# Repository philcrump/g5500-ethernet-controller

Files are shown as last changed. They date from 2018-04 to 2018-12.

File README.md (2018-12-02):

# G-5500 Ethernet Rotator Controller 

This project exists as firmware and a 'shield' board on an ST NUCLEO-STM32F429ZI Development Board.

The firmware exposes a web server on port 80, through which the rotator can be monitored and commanded.

This project is built on ChibiOS 17.6.x with LwIP 1.4.1

<p float="left">
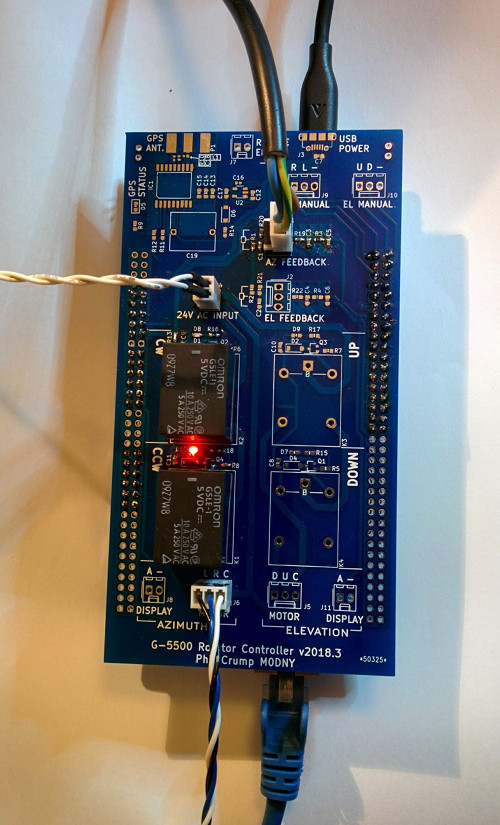
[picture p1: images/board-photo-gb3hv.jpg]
  
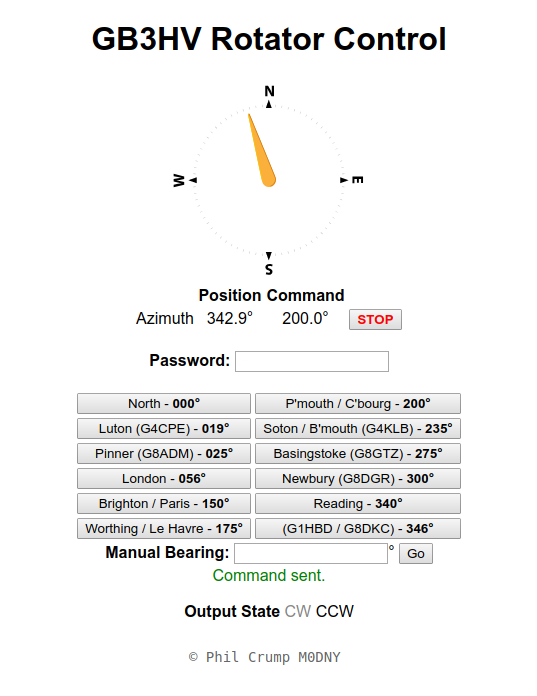
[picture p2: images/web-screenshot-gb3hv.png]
  
</p>

## Wiring

**J1** - "AZ FEEDBACK"
1. G-5500 Azimuth Pin 1 (Feedback Rheostat 360-end)
2. G-5500 Azimuth Pin 2 (Feedback Rheostat Wiper)
3. G-5500 Azimuth Pin 3 (Feedback Rheostat 0-end)

**J6** - "AZIMUTH" -> "MOTOR"
1. (L) G-5500 Azimuth Pin 4 (Motor Winding 1)
2. (R) G-5500 Azimuth Pin 5 (Motor Winding 2)
3. (C) G-5500 Azimuth Pin 6 (Motor Center Tap)

## TODO

- [x] Flash Storage of settings (on settings branch)
- [ ] Interface to edit presets

### Possible future features

- [ ] Merge in satellite tracking computations from old project (using NTP, GPS, & libpredict)
- [ ] Update to ChibiOS 18.2.x (There seems to be a DHCP Client bug - needs investigation)

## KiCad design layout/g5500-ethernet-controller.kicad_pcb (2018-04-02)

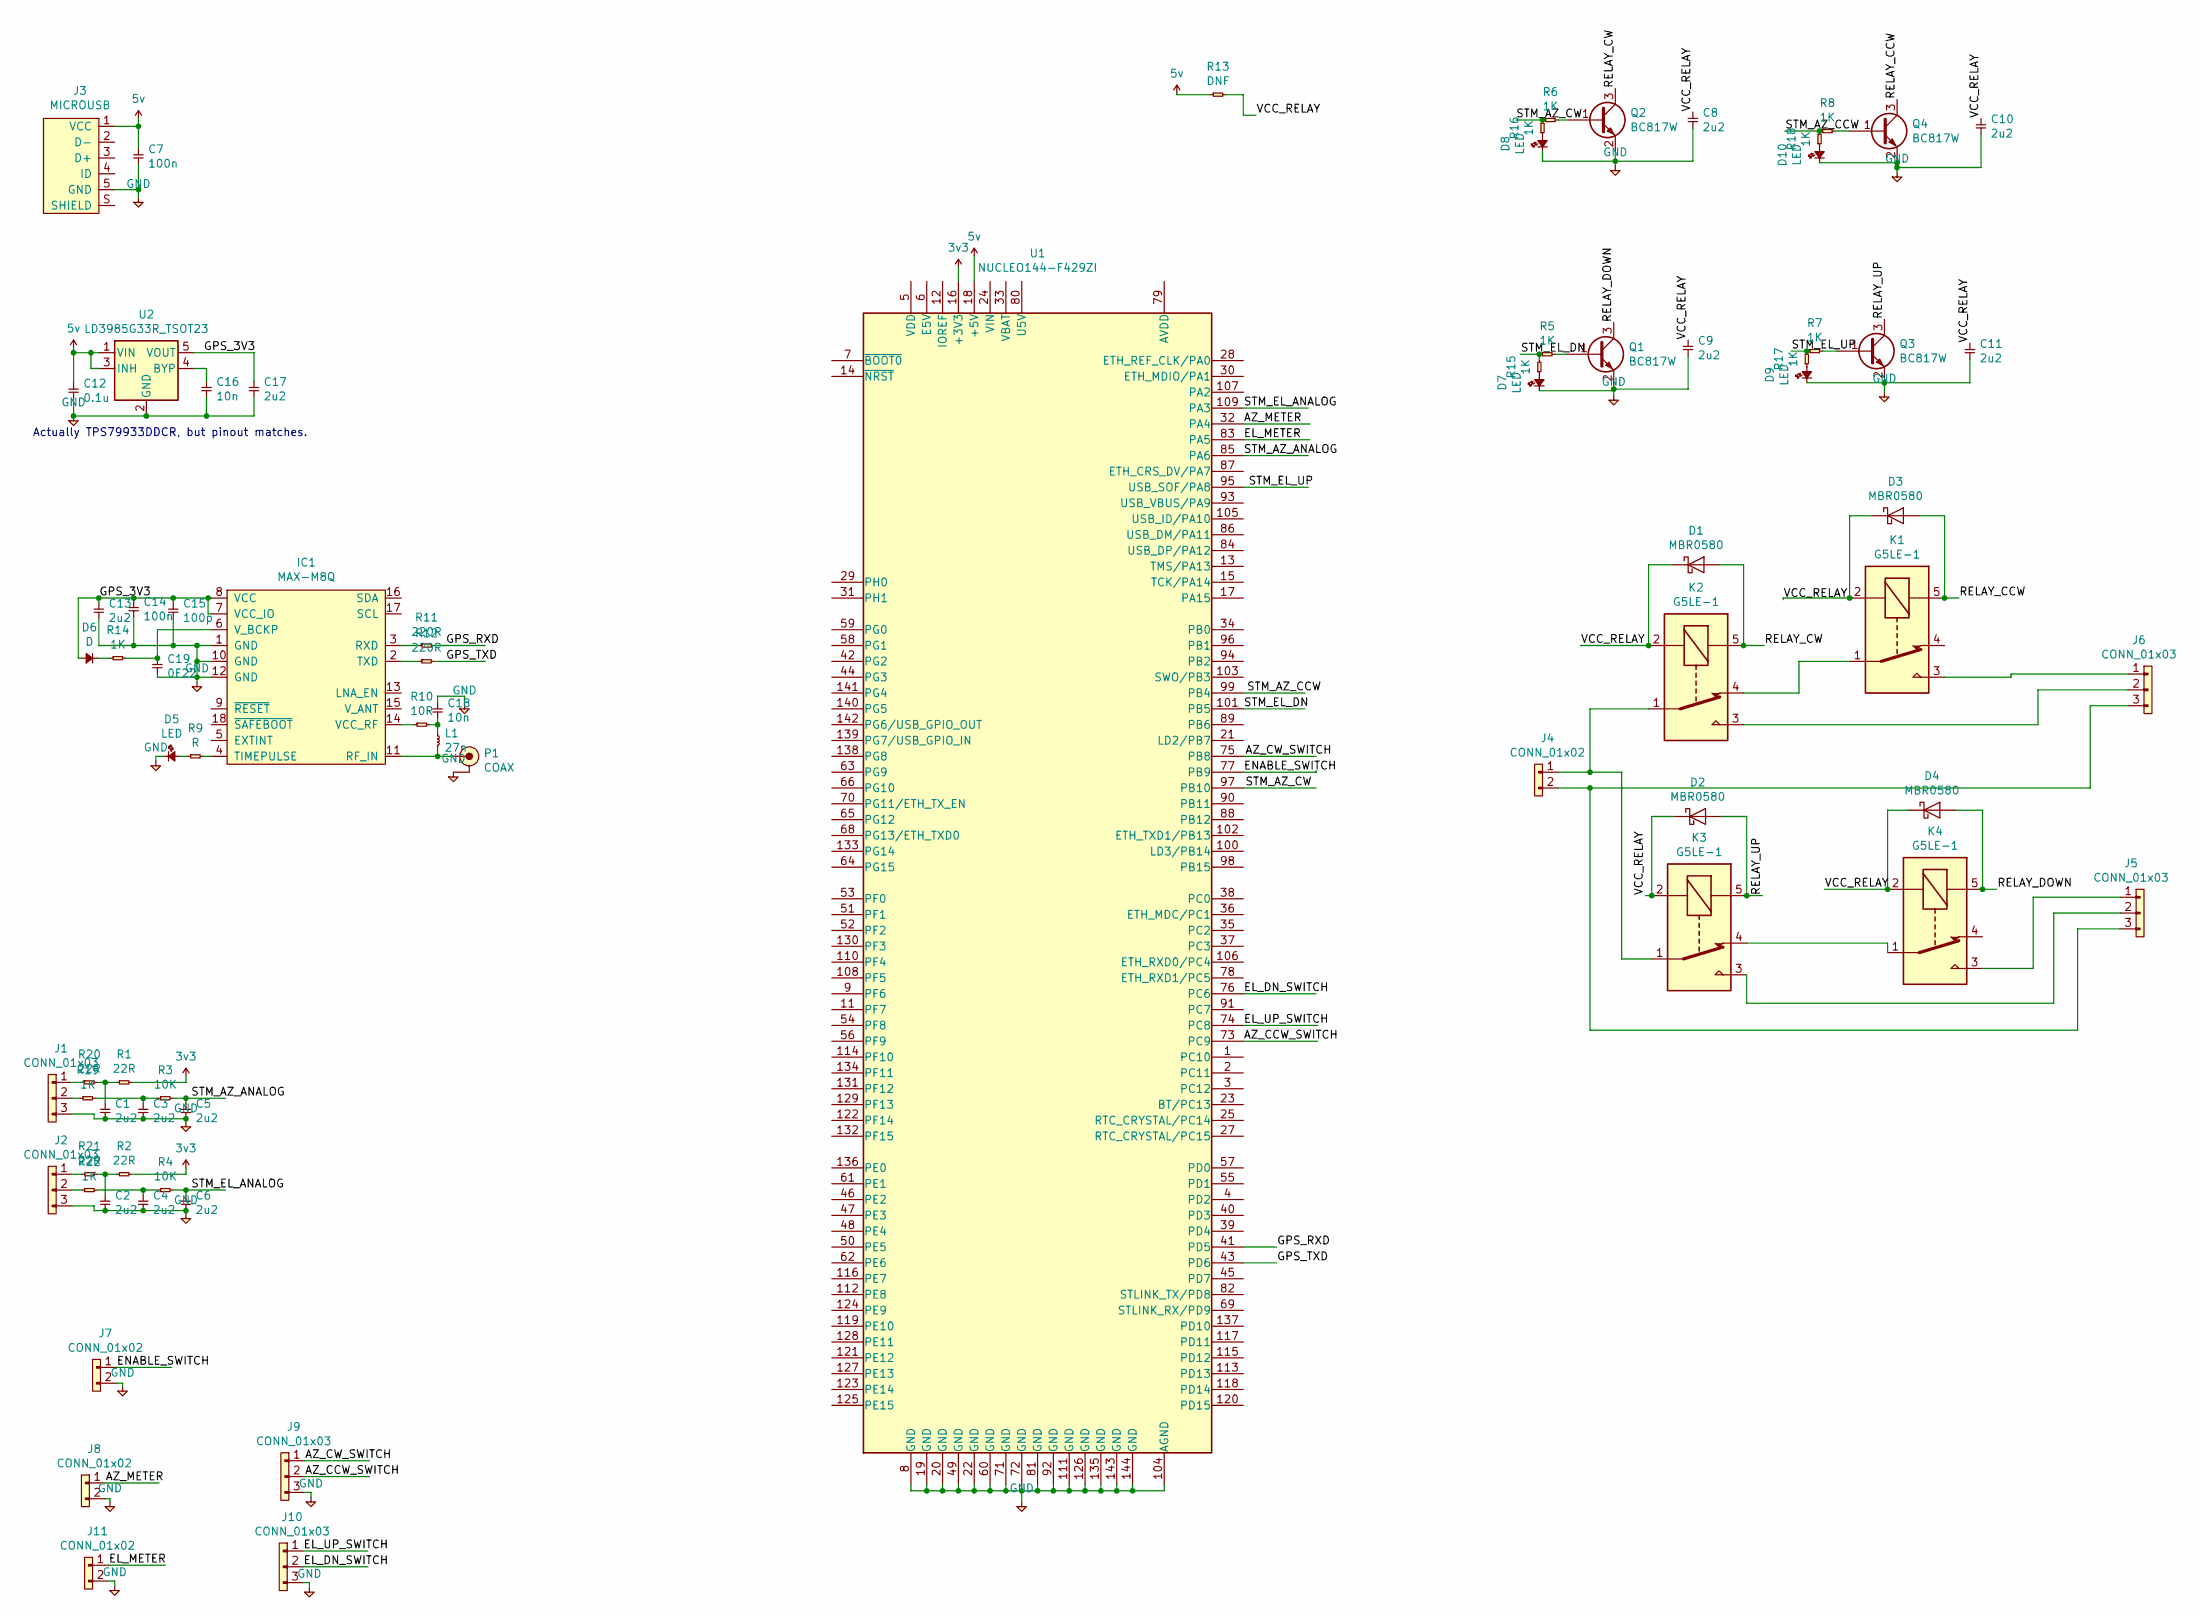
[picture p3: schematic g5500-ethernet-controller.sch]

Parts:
C1, C2, C3, C4, C5, C6, C8, C9, C10, C11, C13, C17: 2u2; 0603
C7, C14: 100n; 0603
C12: 0.1u; 0603
C15: 100p; 0603
C16, C18: 10n; 0402
C19: 0F22; C_Rect_L11.5mm_W9.8mm_P10.00mm_MKT; Farnell_OC 9692690
D1, D2, D3, D4: MBR0580; D_SOD-123
D5, D7, D8, D9, D10: LED; 0603-LED
D6: D; D_SOD-123
IC1: MAX-M8Q
J1, J2, J5, J6, J9, J10: CONN_01x03; Molex_KK-254_AE-6410-03A_1x03_P2.54mm_Vertical
J3: MICROUSB; MICROUSB_MOLEX_47589-0001; Farnell 1568023
J4, J7, J8, J11: CONN_01x02; Molex_KK-254_AE-6410-02A_1x02_P2.54mm_Vertical
K1, K2, K3, K4: G5LE-1; Relay_SPDT_OMRON-G5LE-1
L1: 27n; 0402
P1: COAX; SMA-EDGE; Farnell 1608592
Q1, Q2, Q3, Q4: BC817W; SOT-323_SC-70
R1, R2, R20, R21: 22R; 0603
R3, R4: 10K; 0603
R5, R6, R7, R8, R14, R15, R16, R17, R18, R19, R22: 1K; 0603
R9: R; 0603
R10: 10R; 0402
R11, R12: 220R; 0603
R13: DNF; 0603
U1: NUCLEO144-F429ZI; ST_Morpho_Connector_144_STLink
U2: LD3985G33R_TSOT23; TSOT-23-5

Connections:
3v3: R1.2, R2.2, U1.16 (+3V3)
5v: C7.1, C12.1, J3.1 (VCC), R13.1, U1.18 (+5V), U2.1 (VIN), U2.3 (INH)
/AZ_CCW_SWITCH: J9.2, U1.73 (PC9)
/AZ_CW_SWITCH: J9.1, U1.75 (PB8)
/AZ_METER: J8.1, U1.32 (PA4)
/EL_DN_SWITCH: J10.2, U1.76 (PC6)
/EL_METER: J11.1, U1.83 (PA5)
/EL_UP_SWITCH: J10.1, U1.74 (PC8)
/ENABLE_SWITCH: J7.1, U1.77 (PB9)
/GPS_3V3: C13.1, C14.1, C15.1, C17.1, D6.2, IC1.7 (VCC_IO), IC1.8 (VCC), U2.5 (VOUT)
/GPS_RXD: R11.2, U1.41 (PD5)
/GPS_TXD: R12.2, U1.43 (PD6)
/RELAY_CCW: D3.2 (A), K1.5, Q4.3 (C)
/RELAY_CW: D1.2 (A), K2.5, Q2.3 (C)
/RELAY_DOWN: D4.2 (A), K4.5, Q1.3 (C)
/RELAY_UP: D2.2 (A), K3.5, Q3.3 (C)
/STM_AZ_ANALOG: C5.1, R3.2, U1.85 (PA6)
/STM_AZ_CCW: R8.1, R18.2, U1.99 (PB4)
/STM_AZ_CW: R6.1, R16.2, U1.97 (PB10)
/STM_EL_ANALOG: C6.1, R4.2, U1.109 (PA3)
/STM_EL_DN: R5.1, R15.2, U1.101 (PB5)
/STM_EL_UP: R7.1, R17.2, U1.95 (USB_SOF/PA8)
/VCC_RELAY: C8.1, C9.1, C10.1, C11.1, D1.1 (K), D2.1 (K), D3.1 (K), D4.1 (K), K1.2, K2.2, K3.2, K4.2, R13.2
GND: C1.2, C2.2, C3.2, C4.2, C5.2, C6.2, C7.2, C8.2, C9.2, C10.2, C11.2, C12.2, C13.2, C14.2, C15.2, C16.2, C17.2, C18.1, C19.2, D5.1, D7.1, D8.1, D9.1, D10.1, IC1.1 (GND), IC1.10 (GND), IC1.12 (GND), J1.3, J2.3, J3.5 (GND), J7.2, J8.2, J9.3, J10.3, J11.2, P1.2 (GND), Q1.2 (E), Q2.2 (E), Q3.2 (E), Q4.2 (E), U1.8 (GND), U1.19 (GND), U1.20 (GND), U1.22 (GND), U1.49 (GND), U1.60 (GND), U1.71 (GND), U1.72 (GND), U1.81 (GND), U1.92 (GND), U1.104 (AGND), U1.111 (GND), U1.126 (GND), U1.135 (GND), U1.143 (GND), U1.144 (GND), U2.2 (GND)
unnamed: C1.1, R1.1, R20.2
unnamed: C2.1, R2.1, R21.2
unnamed: C3.1, R3.1, R19.2
unnamed: C4.1, R4.1, R22.2
unnamed: C16.1, U2.4 (BYP)
unnamed: C18.2, L1.1, R10.2
unnamed: C19.1, IC1.6 (V_BCKP), R14.2
unnamed: D5.2, R9.1
unnamed: D6.1, R14.1
unnamed: D7.2, R15.1
unnamed: D8.2, R16.1
unnamed: D9.2, R17.1
unnamed: D10.2, R18.1
unnamed: IC1.2 (TXD), R12.1
unnamed: IC1.3 (RXD), R11.1
unnamed: IC1.4 (TIMEPULSE), R9.2
unnamed: IC1.11 (RF_IN), L1.2, P1.1 (RF)
unnamed: IC1.14 (VCC_RF), R10.1
unnamed: J1.1, R20.1
unnamed: J1.2, R19.1
unnamed: J2.1, R21.1
unnamed: J2.2, R22.1
unnamed: J4.1, K2.1, K3.1
unnamed: J4.2, J5.3, J6.3
unnamed: J5.1, K4.3
unnamed: J5.2, K3.3
unnamed: J6.1, K1.3
unnamed: J6.2, K2.3
unnamed: K1.1, K2.4
unnamed: K3.4, K4.1
unnamed: Q1.1 (B), R5.2
unnamed: Q2.1 (B), R6.2
unnamed: Q3.1 (B), R7.2
unnamed: Q4.1 (B), R8.2

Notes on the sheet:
Actually TPS79933DDCR, but pinout matches.

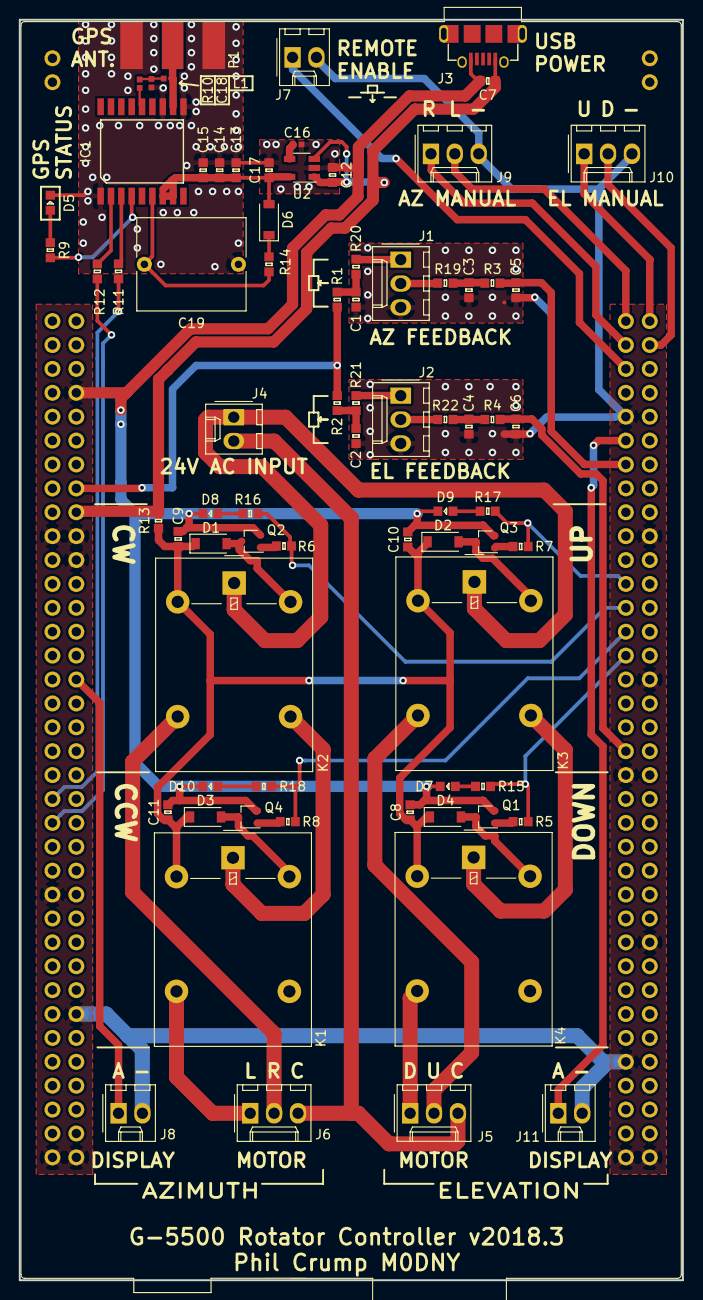
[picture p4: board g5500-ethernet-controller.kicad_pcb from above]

Board: 2 copper layers, 70.5 x 134.0 mm, 75 parts (0 on the bottom side), 58 nets.

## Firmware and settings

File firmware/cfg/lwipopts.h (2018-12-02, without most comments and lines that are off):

#define __LWIPOPT_H__
#define LWIP_HOSTNAME                       "rotator"
#define LWIP_IPADDR(p)                      IP4_ADDR(p, 0, 0, 0, 0)
#define LWIP_GATEWAY(p)                     IP4_ADDR(p, 0, 0, 0, 0)
#define LWIP_NETMASK(p)                     IP4_ADDR(p, 255, 255, 255, 0)
#define LWIP_LINK_POLL_INTERVAL             MS2ST(100)
#define LWIP_TIMEVAL_PRIVATE 0
#define SYS_LIGHTWEIGHT_PROT            0
#define NO_SYS                          0
#define NO_SYS_NO_TIMERS                0
#define MEMCPY(dst,src,len)             memcpy(dst,src,len)
#define SMEMCPY(dst,src,len)            memcpy(dst,src,len)
#define MEM_LIBC_MALLOC                 0
#define MEMP_MEM_MALLOC                 0
#define MEM_ALIGNMENT                   4
#define MEM_SIZE                        1600
#define MEMP_SEPARATE_POOLS             0
#define MEMP_OVERFLOW_CHECK             0
#define MEMP_SANITY_CHECK               0
#define MEM_USE_POOLS                   0
#define MEM_USE_POOLS_TRY_BIGGER_POOL   0
#define MEMP_USE_CUSTOM_POOLS           0
#define LWIP_ALLOW_MEM_FREE_FROM_OTHER_CONTEXT 0
#define MEMP_NUM_PBUF                   16
#define MEMP_NUM_RAW_PCB                4
#define MEMP_NUM_UDP_PCB                6
#define MEMP_NUM_TCP_PCB                6
#define MEMP_NUM_TCP_PCB_LISTEN         8
#define MEMP_NUM_TCP_SEG                16
#define MEMP_NUM_REASSDATA              5
#define MEMP_NUM_FRAG_PBUF              15
#define MEMP_NUM_ARP_QUEUE              30
#define MEMP_NUM_IGMP_GROUP             8
#define MEMP_NUM_SYS_TIMEOUT            (2 + LWIP_TCP + IP_REASSEMBLY + LWIP_ARP + (2*LWIP_DHCP) + LWIP_AUTOIP + LWIP_IGMP + LWIP_DNS + PPP_SUPPORT)
#define MEMP_NUM_NETBUF                 2
#define MEMP_NUM_NETCONN                4
#define MEMP_NUM_TCPIP_MSG_API          8
#define MEMP_NUM_TCPIP_MSG_INPKT        8
#define MEMP_NUM_SNMP_NODE              50
#define MEMP_NUM_SNMP_ROOTNODE          30
#define MEMP_NUM_SNMP_VARBIND           2
#define MEMP_NUM_SNMP_VALUE             3
#define MEMP_NUM_NETDB                  1
#define MEMP_NUM_LOCALHOSTLIST          1
#define MEMP_NUM_PPPOE_INTERFACES       1
#define PBUF_POOL_SIZE                  32 // 16
#define LWIP_ARP                        1
#define ARP_TABLE_SIZE                  10
#define ARP_QUEUEING                    0
#define ETHARP_TRUST_IP_MAC             0
#define ETHARP_SUPPORT_VLAN             0
#define LWIP_ETHERNET                   (LWIP_ARP || PPPOE_SUPPORT)
#define ETH_PAD_SIZE                    0
#define ETHARP_SUPPORT_STATIC_ENTRIES   0
#define IP_FORWARD                      0
#define IP_OPTIONS_ALLOWED              1
#define IP_REASSEMBLY                   1
#define IP_FRAG                         1
#define IP_REASS_MAXAGE                 3
#define IP_REASS_MAX_PBUFS              10
#define IP_FRAG_USES_STATIC_BUF         0
#if IP_FRAG_USES_STATIC_BUF && !defined(IP_FRAG_MAX_MTU)
#define IP_FRAG_MAX_MTU                 1500
#endif
#define IP_DEFAULT_TTL                  255
#define IP_SOF_BROADCAST                0
#define IP_SOF_BROADCAST_RECV           0
#define IP_FORWARD_ALLOW_TX_ON_RX_NETIF 0
#define LWIP_RANDOMIZE_INITIAL_LOCAL_PORTS 0
#define LWIP_ICMP                       1
#define ICMP_TTL                       (IP_DEFAULT_TTL)
#define LWIP_BROADCAST_PING             0
#define LWIP_MULTICAST_PING             0
#define LWIP_RAW                        1
#define RAW_TTL                        (IP_DEFAULT_TTL)
#define LWIP_DHCP                       1
#define LWIP_DHCP_BOOTP_FILE            FALSE
#define DHCP_DOES_ARP_CHECK             ((LWIP_DHCP) && (LWIP_ARP))
#define LWIP_AUTOIP                     0
#define LWIP_DHCP_AUTOIP_COOP           0
#define LWIP_DHCP_AUTOIP_COOP_TRIES     9
#define LWIP_SNMP                       0
#define SNMP_CONCURRENT_REQUESTS        1
#define SNMP_TRAP_DESTINATIONS          1
#define SNMP_PRIVATE_MIB                0
#define SNMP_SAFE_REQUESTS              1
#define SNMP_MAX_OCTET_STRING_LEN       127
#define SNMP_MAX_TREE_DEPTH             15
#define SNMP_MAX_VALUE_SIZE             LWIP_MAX((SNMP_MAX_OCTET_STRING_LEN)+1, sizeof(s32_t)*(SNMP_MAX_TREE_DEPTH))
#define LWIP_IGMP                       0
#define LWIP_DNS                        0
#define DNS_TABLE_SIZE                  4
#define DNS_MAX_NAME_LENGTH             256
#define DNS_MAX_SERVERS                 2
#define DNS_DOES_NAME_CHECK             1
#define DNS_MSG_SIZE                    512
#define DNS_LOCAL_HOSTLIST              0
#define DNS_LOCAL_HOSTLIST_IS_DYNAMIC   0
#define LWIP_UDP                        1
#define LWIP_UDPLITE                    0
#define UDP_TTL                         (IP_DEFAULT_TTL)
#define LWIP_NETBUF_RECVINFO            0
#define LWIP_TCP                        1
#define TCP_TTL                         (IP_DEFAULT_TTL)
#define TCP_WND                         (4 * TCP_MSS)
#define TCP_MAXRTX                      12
#define TCP_SYNMAXRTX                   6
#define TCP_QUEUE_OOSEQ                 (LWIP_TCP)
#define TCP_MSS                         536
#define TCP_CALCULATE_EFF_SEND_MSS      1
#define TCP_SND_BUF                     (2 * TCP_MSS)
#define TCP_SND_QUEUELEN                ((4 * (TCP_SND_BUF) + (TCP_MSS - 1))/(TCP_MSS))
#define TCP_SNDLOWAT                    LWIP_MIN(LWIP_MAX(((TCP_SND_BUF)/2), (2 * TCP_MSS) + 1), (TCP_SND_BUF) - 1)
#define TCP_SNDQUEUELOWAT               LWIP_MAX(((TCP_SND_QUEUELEN)/2), 5)
#define TCP_OOSEQ_MAX_BYTES             0
#define TCP_OOSEQ_MAX_PBUFS             0
#define TCP_LISTEN_BACKLOG              0
#define TCP_DEFAULT_LISTEN_BACKLOG      0xff
#define TCP_OVERSIZE                    TCP_MSS
#define LWIP_TCP_TIMESTAMPS             0
#define TCP_WND_UPDATE_THRESHOLD   (TCP_WND / 4)
#if !defined(LWIP_EVENT_API) && !defined(LWIP_CALLBACK_API)
#define LWIP_EVENT_API                  0
#define LWIP_CALLBACK_API               1
#endif
#define PBUF_LINK_HLEN                  (14 + ETH_PAD_SIZE)
#define PBUF_POOL_BUFSIZE               LWIP_MEM_ALIGN_SIZE(TCP_MSS+40+PBUF_LINK_HLEN)
#define LWIP_NETIF_HOSTNAME             1
#define LWIP_NETIF_API                  0
#define LWIP_NETIF_STATUS_CALLBACK      0
#define LWIP_NETIF_LINK_CALLBACK        1
#define LWIP_NETIF_REMOVE_CALLBACK      0
#define LWIP_NETIF_HWADDRHINT           0
#define LWIP_NETIF_LOOPBACK             0
#define LWIP_LOOPBACK_MAX_PBUFS         0
#define LWIP_NETIF_LOOPBACK_MULTITHREADING    (!NO_SYS)
#define LWIP_NETIF_TX_SINGLE_PBUF             0
#define LWIP_HAVE_LOOPIF                0
#define LWIP_HAVE_SLIPIF                0
#define TCPIP_THREAD_NAME              "tcpip_thread"
#define TCPIP_THREAD_STACKSIZE          1024
#define TCPIP_THREAD_PRIO               (LOWPRIO + 1)
#define TCPIP_MBOX_SIZE                 MEMP_NUM_PBUF
#define SLIPIF_THREAD_NAME             "slipif_loop"
#define SLIPIF_THREAD_STACKSIZE         1024
#define SLIPIF_THREAD_PRIO              (LOWPRIO + 1)
#define PPP_THREAD_NAME                "pppInputThread"
#define PPP_THREAD_STACKSIZE            1024
#define PPP_THREAD_PRIO                 (LOWPRIO + 1)
#define DEFAULT_THREAD_NAME            "lwIP"
#define DEFAULT_THREAD_STACKSIZE        1024
#define DEFAULT_THREAD_PRIO             (LOWPRIO + 1)
#define DEFAULT_RAW_RECVMBOX_SIZE       4
#define DEFAULT_UDP_RECVMBOX_SIZE       4
#define DEFAULT_TCP_RECVMBOX_SIZE       40
#define DEFAULT_ACCEPTMBOX_SIZE         4
#define LWIP_TCPIP_CORE_LOCKING         0
#define LWIP_TCPIP_CORE_LOCKING_INPUT   0
#define LWIP_NETCONN                    1
#define LWIP_TCPIP_TIMEOUT              1
#define LWIP_SOCKET                     1
#define LWIP_COMPAT_SOCKETS             1
#define LWIP_POSIX_SOCKETS_IO_NAMES     1
#define LWIP_TCP_KEEPALIVE              0
#define LWIP_SO_SNDTIMEO                1
#define LWIP_SO_RCVTIMEO                1
#define LWIP_SO_RCVBUF                  0
#define RECV_BUFSIZE_DEFAULT            INT_MAX
#define SO_REUSE                        0
#define SO_REUSE_RXTOALL                0
#define LWIP_STATS                      1
#if LWIP_STATS
#define LWIP_STATS_DISPLAY              0
#define LINK_STATS                      1
#define ETHARP_STATS                    (LWIP_ARP)
#define IP_STATS                        1
#define IPFRAG_STATS                    (IP_REASSEMBLY || IP_FRAG)
#define ICMP_STATS                      1
#define IGMP_STATS                      (LWIP_IGMP)
#define UDP_STATS                       (LWIP_UDP)
#define TCP_STATS                       (LWIP_TCP)
#define MEM_STATS                       ((MEM_LIBC_MALLOC == 0) && (MEM_USE_POOLS == 0))
#define MEMP_STATS                      (MEMP_MEM_MALLOC == 0)
#define SYS_STATS                       (NO_SYS == 0)
#else
#define LINK_STATS                      0
#define IP_STATS                        0
#define IPFRAG_STATS                    0
#define ICMP_STATS                      0
#define IGMP_STATS                      0
#define UDP_STATS                       0
#define TCP_STATS                       0
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

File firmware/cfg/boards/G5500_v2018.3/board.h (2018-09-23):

/*
    ChibiOS - Copyright (C) 2006..2018 Giovanni Di Sirio

    Licensed under the Apache License, Version 2.0 (the "License");
    you may not use this file except in compliance with the License.
    You may obtain a copy of the License at

        http://www.apache.org/licenses/LICENSE-2.0

    Unless required by applicable law or agreed to in writing, software
    distributed under the License is distributed on an "AS IS" BASIS,
    WITHOUT WARRANTIES OR CONDITIONS OF ANY KIND, either express or implied.
    See the License for the specific language governing permissions and
    limitations under the License.
*/

/*
 * This file has been automatically generated using ChibiStudio board
 * generator plugin. Do not edit manually.
 */

#ifndef BOARD_H
#define BOARD_H

/*===========================================================================*/
/* Driver constants.                                                         */
/*===========================================================================*/

/*
 * Setup for STMicroelectronics STM32 Nucleo144-F429ZI board.
 */

/*
 * Board identifier.
 */
#define BOARD_ST_NUCLEO144_F429ZI
#define BOARD_NAME                  "ST STM32 Nucleo144-F429ZI"

/*
 * Ethernet PHY type.
 */
#define BOARD_PHY_ID                MII_LAN8742A_ID
#define BOARD_PHY_RMII

/*
 * Board oscillators-related settings.
 * NOTE: LSE not fitted.
 */
#if !defined(STM32_LSECLK)
#define STM32_LSECLK                0U
#endif

#if !defined(STM32_HSECLK)
#define STM32_HSECLK                8000000U
#endif

#define STM32_HSE_BYPASS

/*
 * Board voltages.
 * Required for performance limits calculation.
 */
#define STM32_VDD                   300U

/*
 * MCU type as defined in the ST header.
 */
#define STM32F429xx

/*
 * IO pins assignments.
 */
#define GPIOA_ZIO_D32               0U
#define GPIOA_TIM2_CH1              0U
#define GPIOA_RMII_REF_CLK          1U
#define GPIOA_RMII_MDIO             2U
#define GPIOA_ARD_A0                3U
#define GPIOA_ADC123_IN3            3U
#define GPIOA_ZIO_D24               4U
#define GPIOA_SPI3_NSS              4U
#define GPIOA_ARD_D13               5U
#define GPIOA_SPI1_SCK              5U
#define GPIOA_ARD_D12               6U
#define GPIOA_SPI1_MISO             6U
#define GPIOA_ARD_D11               7U
#define GPIOA_SPI1_MOSI             7U
#define GPIOA_ZIO_D71               7U
#define GPIOA_RMII_RX_DV            7U
#define GPIOA_USB_SOF               8U
#define GPIOA_USB_VBUS              9U
#define GPIOA_USB_ID                10U
#define GPIOA_USB_DM                11U
#define GPIOA_USB_DP                12U
#define GPIOA_SWDIO                 13U
#define GPIOA_SWCLK                 14U
#define GPIOA_ZIO_D20               15U
#define GPIOA_I2S3_WS               15U

#define GPIOB_ZIO_D33               0U
#define GPIOB_TIM3_CH3              0U
#define GPIOB_LED1                  0U
#define GPIOB_ZIO_A6                1U
#define GPIOB_ADC12_IN9             1U
#define GPIOB_ZIO_D27               2U
#define GPIOB_ZIO_D23               3U
#define GPIOB_I2S3_CK               3U
#define GPIOB_ZIO_D25               4U
#define GPIOB_SPI3_MISO             4U
#define GPIOB_ZIO_D22               5U
#define GPIOB_I2S3_SD               5U
#define GPIOB_ZIO_D26               6U
#define GPIOB_LED2                  7U
#define GPIOB_ARD_D15               8U
#define GPIOB_I2C1_SCL              8U
#define GPIOB_ARD_D14               9U
#define GPIOB_I2C1_SDA              9U
#define GPIOB_ZIO_D36               10U
#define GPIOB_TIM2_CH3              10U
#define GPIOB_ZIO_D35               11U
#define GPIOB_TIM2_CH4              11U
#define GPIOB_ZIO_D19               12U
#define GPIOB_I2S2_WS               12U
#define GPIOB_ZIO_D18               13U
#define GPIOB_I2S2_CK               13U
#define GPIOB_RMII_TXD1             13U
#define GPIOB_LED3                  14U
#define GPIOB_ZIO_D17               15U
#define GPIOB_I2S2_SD               15U

#define GPIOC_ARD_A1                0U
#define GPIOC_ADC123_IN10           0U
#define GPIOC_RMII_MDC              1U
#define GPIOC_ZIO_A7                2U
#define GPIOC_ADC123_IN12           2U
#define GPIOC_ARD_A2                3U
#define GPIOC_ADC123_IN13           3U
#define GPIOC_RMII_RXD0             4U
#define GPIOC_RMII_RXD1             5U
#define GPIOC_ZIO_D16               6U
#define GPIOC_I2S2_MCK              6U
#define GPIOC_ZIO_D21               7U
#define GPIOC_I2S3_MCK              7U
#define GPIOC_ZIO_D43               8U
#define GPIOC_SDMMC_D0              8U
#define GPIOC_ZIO_D44               9U
#define GPIOC_SDMMC_D1              9U
#define GPIOC_ZIO_D45               10U
#define GPIOC_SDMMC_D2              10U
#define GPIOC_ZIO_D46               11U
#define GPIOC_SDMMC_D3              11U
#define GPIOC_ZIO_D47               12U
#define GPIOC_SDMMC_CK              12U
#define GPIOC_BUTTON                13U
#define GPIOC_OSC32_IN              14U
#define GPIOC_OSC32_OUT             15U
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

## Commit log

2018-02-19 Layout: Add start of work.
    [g5500-ethernet-controller.kicad_pcb, g5500-ethernet-controller.sch]
2018-02-20 layout: Schematic poking, drag in components used in etherswitch.
    [g5500-ethernet-controller.sch]
2018-03-25 Progress on layout.
    [g5500-ethernet-controller.kicad_pcb, g5500-ethernet-controller.sch]
2018-03-26 Layout nearly done.
    [g5500-ethernet-controller.kicad_pcb, g5500-ethernet-controller.sch]
2018-04-02 layout: Finish and send off v1.
    [g5500-ethernet-controller-B.Cu.gbl, g5500-ethernet-controller-B.Mask.gbs, g5500-ethernet-controller-B.Paste.gbp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]
2018-09-24 Track fw work.
2018-09-24 layout: Add BOM.
2018-10-31 Fixi build for 17.6 (not run).
    [board.c, chconf.h, halconf.h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]
2018-12-02 Mutex on tracking state, misc fixes and tweaks.
    [lwipopts.h, tracking.c]
2022-03-12 web/index.html: Update bearing presets.
2022-03-12 firmware/tracking: Put in calibration values for newer G-5500 (tested).

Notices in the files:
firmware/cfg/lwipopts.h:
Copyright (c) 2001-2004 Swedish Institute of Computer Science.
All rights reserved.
